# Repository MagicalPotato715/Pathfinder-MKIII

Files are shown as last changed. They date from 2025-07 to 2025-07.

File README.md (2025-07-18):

 ****PATHFINDER: MARK III****

-----

About: This is the PCB for the third generation of my project, Pathfinder. The goal for Pathfinder is to make a hexapod walking robot that is able to traverse in diverse and rugged terrain where conventional vehicles (e.g., cars, rovers) prove inefficient. The third generation of Pathfinder (Mark III) will feature significant upgrades from its predecessor (Mark II), including improved motors for speed and weight-bearing, an onboard 7.4V LiPo battery for tetherless power, an accelerometer, and an NRF chip for wireless communication.

Why: I began Pathfinder after my physics teacher encouraged me to join my school's science fair. I had always had an idea for a spider robot that I kept at the back of my mind, but this pushed me to bring it to life. Over the next few weeks, I poured hours every day into learning more about mechanical and electrical engineering. I also sought mentorship from the UC Berkeley Engineering Department and got connected with a Mech E & EECS graduate student.  Mark I of Pathfinder, a simple prototype/proof of concept, was churned out after 2 weeks, just in time for my district's science fair to win me 2nd place. Mark II was developed a few weeks later for the regional science fair. Mark III, the model this PCB is for, will be the culmination of my work over an entire year to be entered into next season's science fair.

(Note: The CAD model was created and fine-tuned over the course 3+ months that were before Highway began, so I didn't record the process in the journals.)

---

**In Depth: How It Works** (for all yall nerds out there)

- **PCB**
  - The PCB is, in essence, a servo driver. It is supposed to be placed on top of a Nucleo F446RE board, taking advantage of its Morpho pins that expose the MCU. The power comes in from a 7.4V 2S LiPo battery connected to the onboard XT60 (just a connector).
  - **Servos** Since the potential ampage could go up to ~10-15A, a pour is used to connect the battery to the 3 buck converters. Each buck converter steps down the battery power from 7.4V to 6V at 5A for 6 servos (two legs). This connection from the buck converters to the servo rails is led by another set of pours. The servos receive PWM input from 15 pins on the right morpho pins and 3 on the left.
  - **Power** The VIN from the XT60 is also connected to the F446RE's onboard VIN pin (it already has a regulator to step down to 3.3V). This power then comes out of the 3.3V pin and is fed to the NRF Chip and the Accelerometer.
  - **Accelerometer** The accelerometer used is the BNO055, an "INTELLIGENT ABSOLUTE ORIENTATION SENSOR, 9-AXIS SENSOR FUSION" (aka gyroscope & accelerometer and prob 9 other things). The BNO055 uses I2C and is connected to SDA & SCL. There is also a manual reset button connected to RST on the BNO055 just for funsies.
  - **NRF Chip** This is going to be used to communicate with the hand-held controller (to be made later). The NRF Chip is the NRF24L01_Breakout. NRF24L01_Breakout uses SPI and thus the MISO, MOSI, CSN, SCK, and CE pins on the F446RE (used on the left morpho pins).
  
- **Body**
  In-depth desc WIP
---

Screenshot 2025-07-18 at 9 36 13 AM  

Screenshot 2025-07-08 at 11 05 50 AM

Screenshot 2025-07-18 at 9 31 08 AM

Screenshot_2025-05-13_at_6 30 04_PM

|Component|Quantity|Model|Lowest Price|Link|
|---|---|---|---|---|
|LED|2|VLMR233T2V2-GS08|$0.35|[Link](https://www.aliexpress.com/item/1005008128628087.html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)|
|Button|2 (1x20pcs)|TL1240NQ1JBLK|$1.27|[Link](https://www.aliexpress.com/item/1005003938985112.html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)|
|Servo Motor|18 (2x10pcs)|MG996R|$30.81|[Link](https://www.aliexpress.com/item/1005007032811340.html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)|
|10uF Capacitor|7 (1x100pcs)|0805W106K250CC|$0.6|[Link](https://www.aliexpress.com/item/1626652703.html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)|
|10k Resistor|5 (1x100pcs)|CR0805-JW-103ELF|$0.35|[Link](https://www.aliexpress.com/item/1005006269805332.html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)|
|500 Resistor|2 (1x100pcs)|CR0805-FX-4990ELF|$0.35|[Link](https://www.aliexpress.com/item/1005006269805332.html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)|
|NRF Board|1|NRF24L01_Breakout|$0.58|[Link](https://www.aliexpress.com/item/1005005642753224.html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)|
|Schottky Resistor|3 (1x20pcs)|MBR1045S|$2.38|[Link](https://www.aliexpress.com/item/3256807600787150.html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)|
|Buck Converter|3 (1x5pcs)|RT8289GSP|$2.26|[Link](https://www.aliexpress.com/item/1005006319216009.html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)|
|47uF Capacitor|6 (1x10pcs)|6TAB47M|$10.30|[Link](https://www.aliexpress.com/item/3256807390659102.html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)|
|39k Resistor|3 (1x100pcs)|CR0805-FX-3832ELF|$0.35|[Link](https://www.aliexpress.com/item/1005006269805332.html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)|
|Developement Board|1|Nucleo F446RE|$25.13|[Link](https://www.aliexpress.com/item/3256808854818208.html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)|
|10uH Inductor|3 (1x10pcs)|EXL1V0505-100-R|$2.43|[Link](https://www.aliexpress.com/item/1005007254030376.html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)|
|XT60 Connector|1|XT60-M|$0.39|[Link](https://www.aliexpress.com/item/1005007103438736.html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)|
|Battery|1|7.4v 2s Lipo|$29.49|[Link](https://www.aliexpress.com/item/3256802810308498.html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)|
|0.1uF Capacitor|3 (1x100pcs)|0603B104K250SD|$0.95|[Link](https://www.aliexpress.com/item/1005003512666695.html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)|
|Accelerometer|1|BNO055|$29.32|[Link](https://www.aliexpress.com/item/3256809169239048.html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)|
|Female Headers|2 (1x10pcs)|PPPC192LFBN-RC|$0.89|[Link](https://www.aliexpress.com/item/4001198421663.html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)|
|Male Headers|18 (1x50pcs)|TS-103-G-A|$0.94|[Link](https://www.aliexpress.com/item/4000988113226.html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)|
|PCB Board|1| |$76.88|JLCPCB Order|

Total Components Price (+26.63 Shipping & tax): $223.39
PCB Price: $76.88
Total Price: $280.27

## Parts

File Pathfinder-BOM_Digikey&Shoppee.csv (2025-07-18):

Component | Quantity | Model | Lowest Price (unit) | Subtotal | Link
LED | 2 | VLMR233T2V2-GS08 | 0.51 | 1.02 | https://www.digikey.tw/en/products/detail/vishay-semiconductor-opto-division/VLMR233T2V2-GS08/3025490
Button | 2 | TL1240NQ1JBLK | 0.98 | 1.96 | https://www.digikey.tw/en/products/detail/e-switch/TL1240NQ1JBLK/1805479
Servo Motor | 18 | MG996R | 4.2 | 75.60 | https://tw.shp.ee/tT3prQu
10uF Capacitor | 7 | 0805W106K250CC | 0.04 | 0.28 | https://tw.shp.ee/vY3ZYgh
10k Resistor | 5 | CR0805-JW-103ELF | 0.10 | 0.50 | https://www.digikey.tw/en/products/detail/bourns-inc/CR0805-JW-103ELF/3593155
500 Resistor | 2 | CR0805-FX-4990ELF | 0.10 | 0.20 | https://www.digikey.tw/en/products/detail/bourns-inc/CR0805-FX-4990ELF/3784987
NRF Board | 1 | NRF24L01_Breakout | 1.00 | 1.00 | https://tw.shp.ee/tFocrzP
Schottky Resistor | 3 | MBR1045S | 1.07 | 3.21 | https://www.digikey.tw/en/products/detail/smc-diode-solutions/MBR1045S/5993230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
Buck Converter | 3 | RT8289GSP | 4.11 | 12.33 | https://www.digikey.tw/en/products/detail/richtek-usa-inc/RT8289GSP/2546068?s=N4IgTCBcDaIEoBUAcYkE4QF0C%2BQ
47uF Capacitor | 6 | 6TAB47M | 1.66 | 9.96 | https://www.digikey.tw/en/products/detail/panasonic-electronic-components/6TAB47M/4833040
38k Resistor | 3 | CR0805-FX-3832ELF | 0.10 | 0.30 | https://www.digikey.tw/en/products/detail/bourns-inc/CR0805-FX-3832ELF/3784908
Developement Board | 1 | NUCLEO-F446RE | 14.85 | 14.85 | https://www.digikey.tw/en/products/detail/stmicroelectronics/NUCLEO-F446RE/5347712
10uH Inductor | 3 | EXL1V0505-100-R | 0.69 | 2.07 | https://www.digikey.tw/en/products/detail/eaton-electronics-division/EXL1V0505-100-R/13912336
XT60 Connector | 1 | XT60-F | 1.57 | 1.57 | https://tw.shp.ee/Gx2Y8iE
0.1uF Capacitor | 3 | 0603B104K250SD | 1.70 | 5.10 | https://tw.shp.ee/weARm6H
Accelerometer | 1 | BNO055 | 38.46 | 38.46 | https://tw.shp.ee/19Ezxnb
Female Headers | 2 | PPPC192LFBN-RC | 2.05 | 4.1 | https://www.digikey.tw/en/products/detail/sullins-connector-solutions/PPPC192LFBN-RC/810258
Male Headers | 18 | TS-103-G-A | 1.27 | 22.86 | https://www.digikey.tw/en/products/detail/samtec-inc/TS-103-G-A/1105459
PCB Board | 1 |  | 76.88 | JLCPCB Order
Total |  |  |  | 245.29

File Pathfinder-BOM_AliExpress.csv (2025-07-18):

Component | Quantity | Model | Lowest Price | Link
LED | 2 | VLMR233T2V2-GS08 | $0.35 | https://www.aliexpress.com/item/1005008128628087.html
Button | 2 (1x20pcs) | TL1240NQ1JBLK | $1.27 | https://www.aliexpress.com/item/1005003938985112.html
Servo Motor | 18 (2x10pcs) | MG996R | $30.81 | https://www.aliexpress.com/item/1005007032811340.html
10uF Capacitor | 7 (1x100pcs) | 0805W106K250CC | $0.60 | https://www.aliexpress.com/item/1626652703.html
10k Resistor | 5 (1x100pcs) | CR0805-JW-103ELF | $0.35 | https://www.aliexpress.com/item/1005006269805332.html
500 Resistor | 2 (1x100pcs) | CR0805-FX-4990ELF | $0.35 | https://www.aliexpress.com/item/1005006269805332.html
NRF Board | 1 | NRF24L01_Breakout | $0.58 | https://www.aliexpress.com/item/1005005642753224.html
Schottky Resistor | 3 (1x20pcs) | MBR1045S | $2.38 | https://www.aliexpress.com/item/3256807600787150.html
Buck Converter | 3 (1x5pcs) | RT8289GSP | $2.26 | https://www.aliexpress.com/item/1005006319216009.html
47uF Capacitor | 6 (1x10pcs) | 6TAB47M | $10.30 | https://www.aliexpress.com/item/3256807390659102.html
39k Resistor | 3 (1x100pcs) | CR0805-FX-3832ELF | $0.35 | https://www.aliexpress.com/item/1005006269805332.html
Developement Board | 1 | Nucleo F446RE | $25.13 | https://www.aliexpress.com/item/3256808854818208.html
10uH Inductor | 3 (1x10pcs) | EXL1V0505-100-R | $2.43 | https://www.aliexpress.com/item/1005007254030376.html
XT60 Connector | 1 | XT60-M | $0.39 | https://www.aliexpress.com/item/1005007103438736.html
Battery | 1 | 7.4v 2s Lipo | $29.49 | https://www.aliexpress.com/item/3256802810308498.html
0.1uF Capacitor | 3 (1x100pcs) | 0603B104K250SD | $0.95 | https://www.aliexpress.com/item/1005003512666695.html
Accelerometer | 1 | BNO055 | $29.32 | https://www.aliexpress.com/item/3256809169239048.html
Female Headers | 2 (1x10pcs) | PPPC192LFBN-RC | $0.89 | https://www.aliexpress.com/item/4001198421663.html
Male Headers | 18 (1x50pcs) | TS-103-G-A | $0.94 | https://www.aliexpress.com/item/4000988113226.html
PCB Board | 1 |  | $76.88 | JLCPCB Order
Total |  |  | $280.27

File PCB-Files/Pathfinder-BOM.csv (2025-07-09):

Id | Designator | Footprint | Quantity | Designation | Supplier and ref
1 | D4,D5 | LED_miniPLCC_2315_Handsoldering | 2 | LED
2 | SW2,SW1 | SW_PUSH_6mm_H9.5mm | 2 | SW_Push
3 | Coxa2,Femur1,Tibia5,Tibia1,Femur3,Coxa4,Coxa5,Tibia3,Tibia2,Coxa3,Femur6,Femur4,Tibia4,Coxa6,Coxa1,Tibia6,Femur5,Femur2 | PinHeader_1x03_P2.54mm_Vertical | 18 | Motor_Servo
4 | C8,C5,C7,C13,C16,C4,C12 | C_0805_2012Metric | 7 | 10uF
5 | R7,R6,R4,R8,R2 | R_0805_2012Metric | 5 | 10k
6 | R9,R10 | R_0805_2012Metric | 2 | 500
7 | U2 | nRF24L01_Breakout | 1 | NRF24L01_Breakout
8 | D7,D1,D3 | MBR1045S | 3 | D_Schottky
9 | BuckConverterB1,BuckConverterC1,BuckConverterA1 | SOIC127P599X175-9N | 3 | ~
10 | C2,C3,C9,C15,C10,C14 | CAP_TA_B2_PAN | 6 | 47uF
11 | R5,R1,R3 | R_0805_2012Metric | 3 | 38k
12 | U1 | MODULE_NUCLEO-F446RE | 1 | NUCLEO-F446RE
13 | L3,L1,L2 | IND_EXL1V0505-100-R_COB | 3 | 10uH
14 | J1 | AMASS_XT60-M | 1 | XT60-M
15 | C11,C6,C1 | C_0603_1608Metric | 3 | 0.1uF
16 | Bno055 | BNO055 | 1 | ~

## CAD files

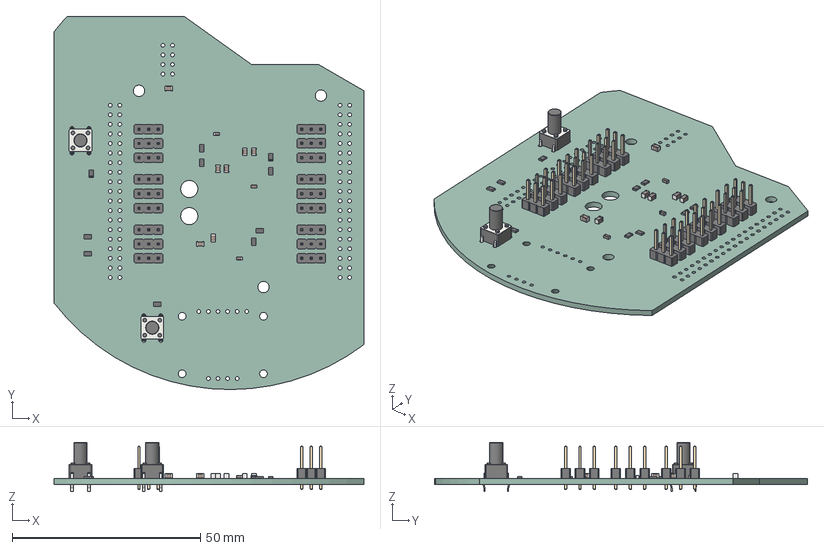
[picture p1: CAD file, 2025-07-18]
PCB-Files/Pathfinder.step
82.2 x 99.0 x 13.0 mm
SW_PUSH_6mm_H9.5mm x 2
PinHeader_1x03_P2.54mm_Vertical x 18
C_0805_2012Metric x 7
R_0805_2012Metric x 10
C_0603_1608Metric x 3
Pathfinder_PCB

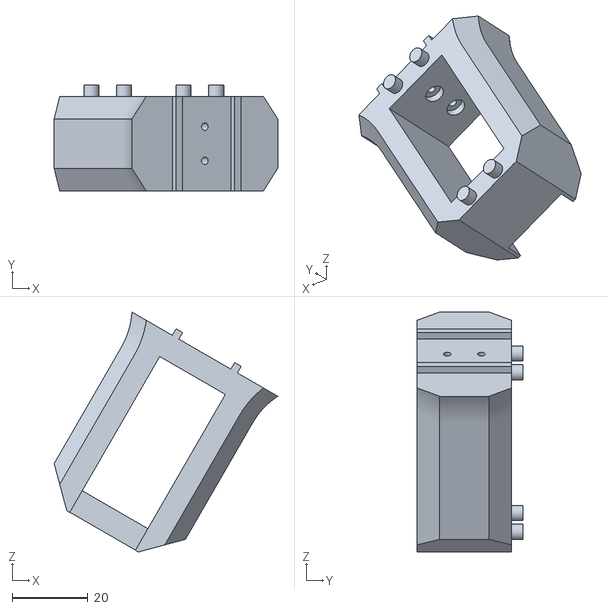
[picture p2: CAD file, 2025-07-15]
CAD-Files/Center Piece Copy 1 - Part 3.stl
59.0 x 28.0 x 63.3

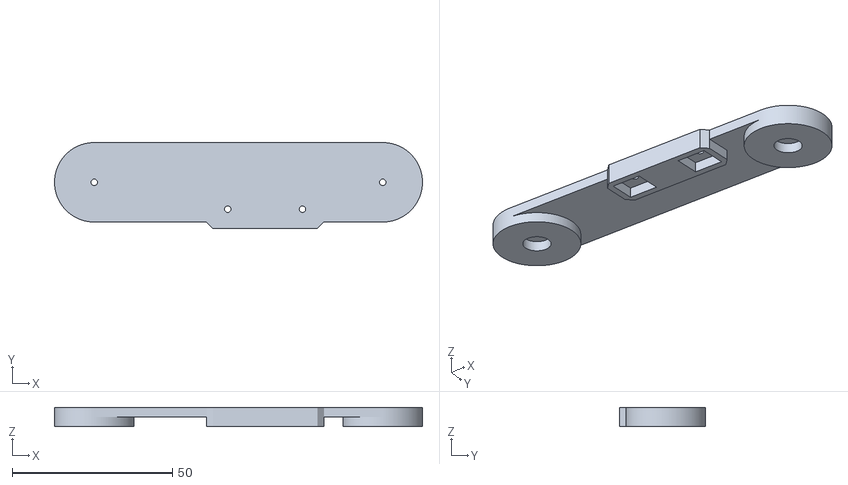
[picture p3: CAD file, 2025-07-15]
CAD-Files/Femur - Part 2.stl
114.8 x 26.8 x 6.00

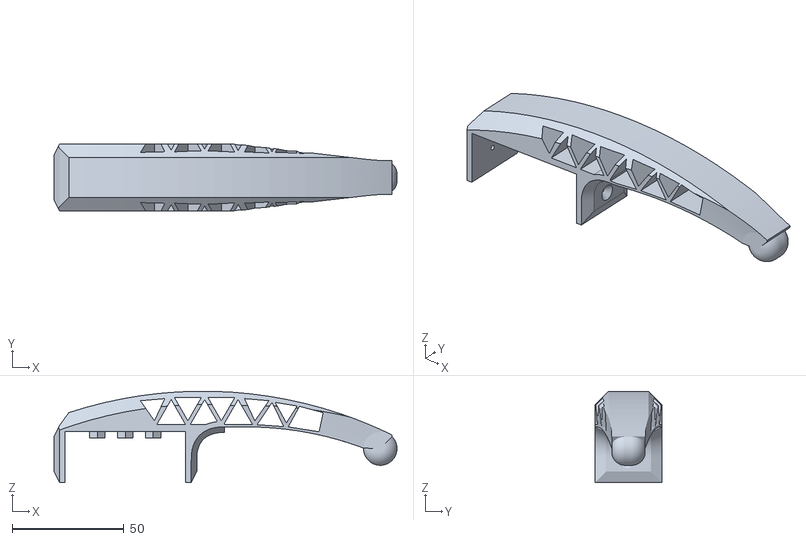
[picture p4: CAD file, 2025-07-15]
CAD-Files/Tibia.stl
153.7 x 30.0 x 41.0

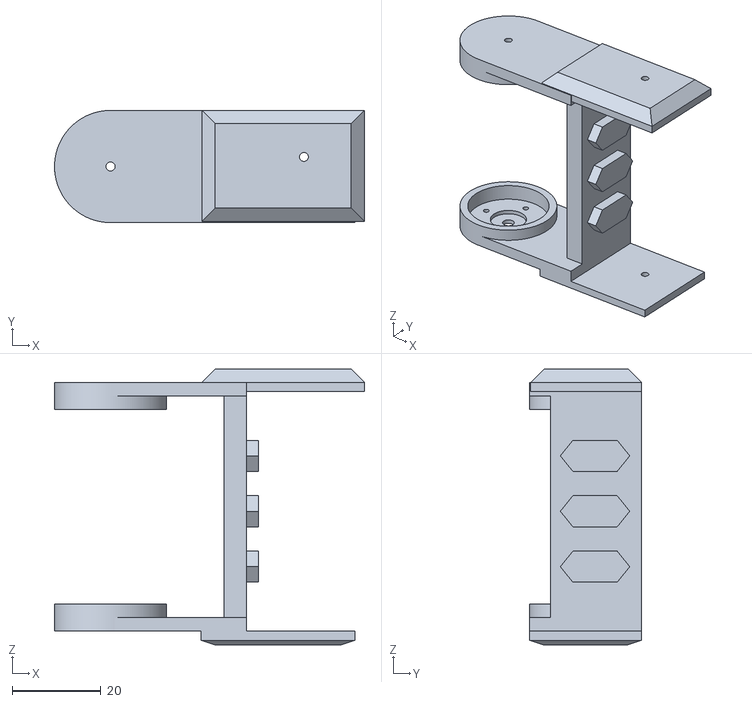
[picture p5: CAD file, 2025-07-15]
CAD-Files/Coxa - Part 4 (4).stl
69.9 x 25.3 x 62.2

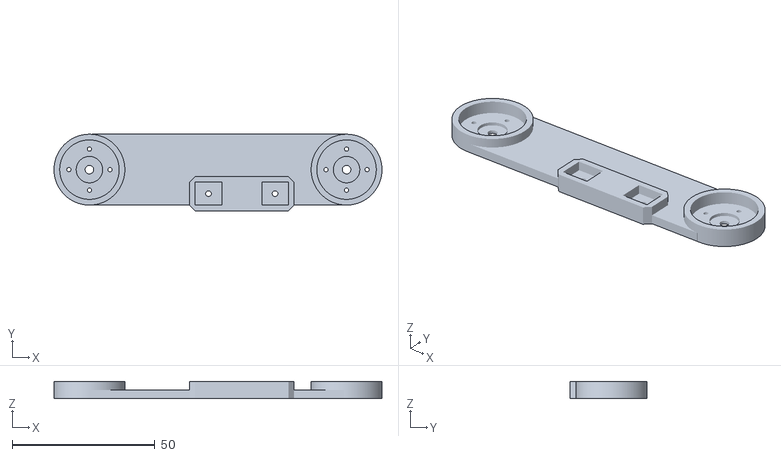
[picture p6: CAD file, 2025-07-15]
CAD-Files/Femur - Part 4.stl
114.8 x 26.8 x 6.00

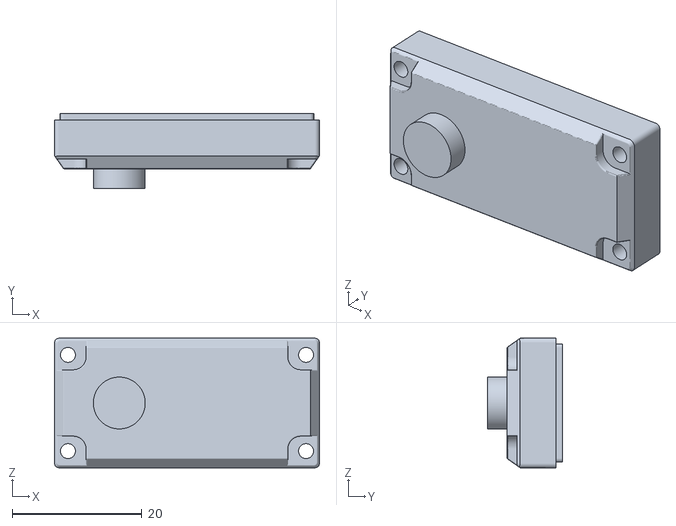
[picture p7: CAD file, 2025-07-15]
CAD-Files/Case Updated.stl
40.9 x 11.5 x 20.0

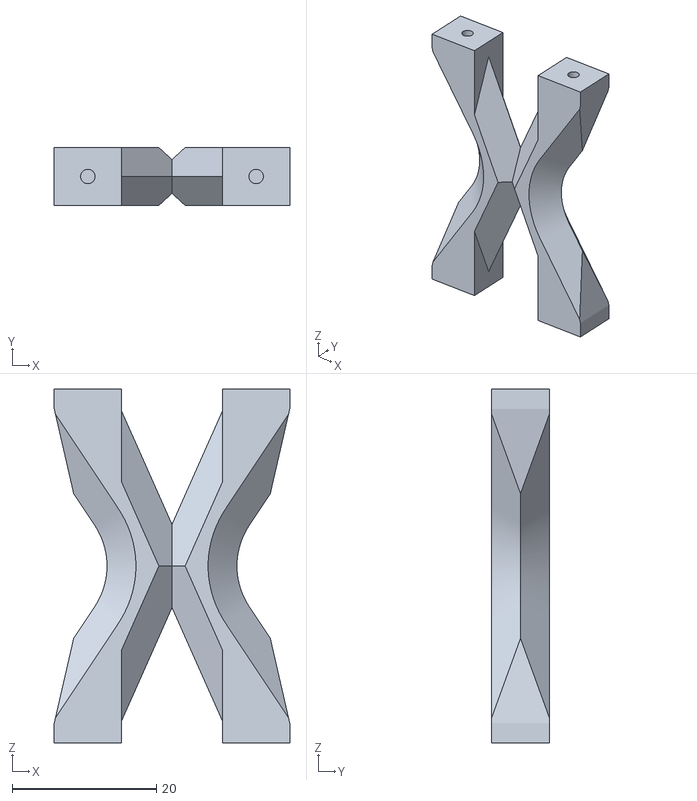
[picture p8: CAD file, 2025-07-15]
CAD-Files/Femur - Part 3.stl
32.6 x 8.00 x 49.0

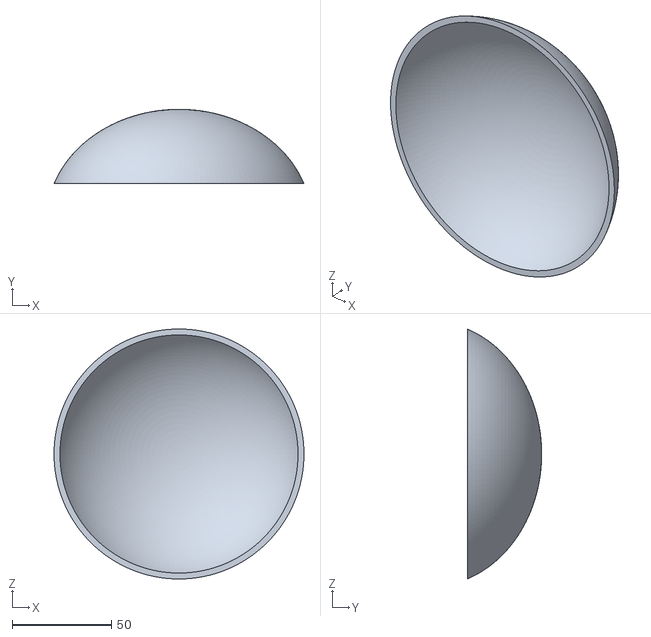
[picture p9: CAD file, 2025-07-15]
CAD-Files/Center Piece Copy 1 - Part 1.stl
126.0 x 37.5 x 126.0

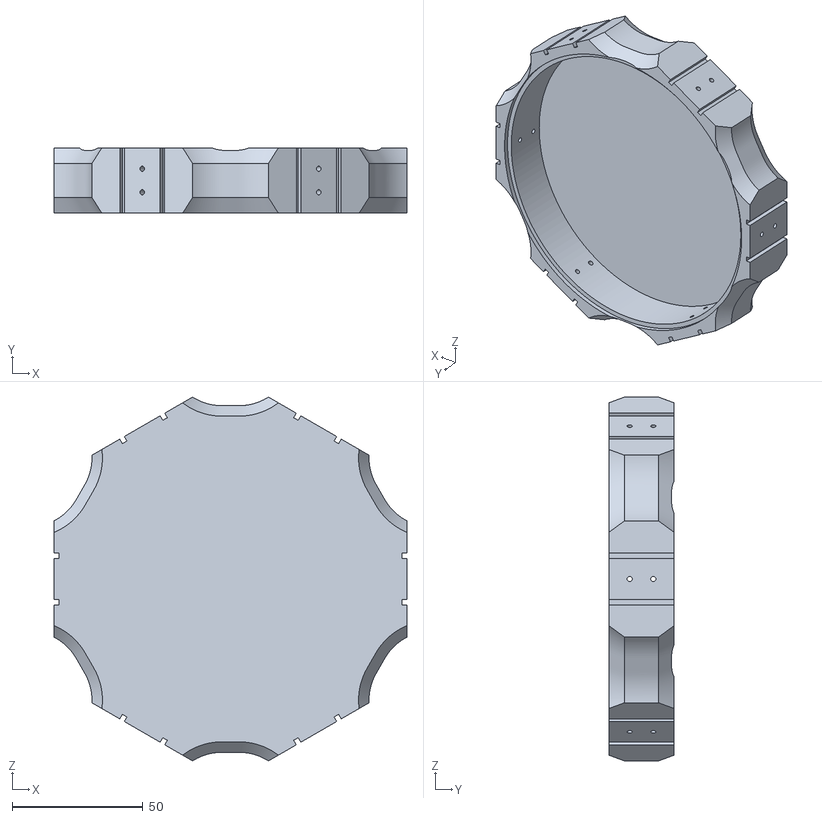
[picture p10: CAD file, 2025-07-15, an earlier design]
CAD-Files/Center Piece Copy 1 - Part 3 (4).stl
135.0 x 25.0 x 139.2

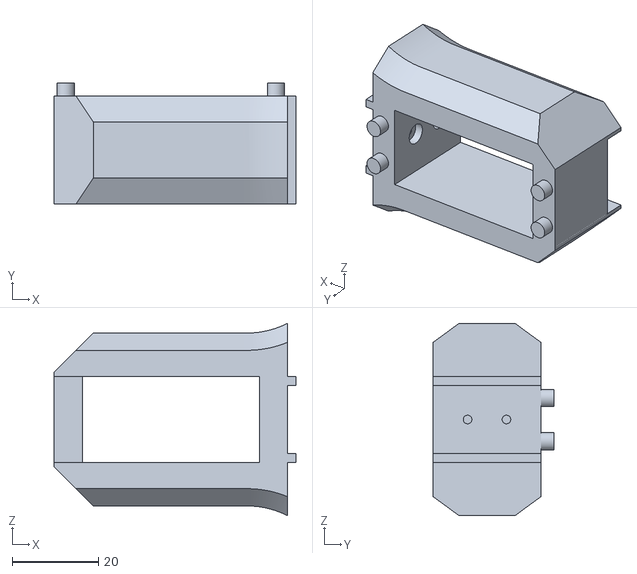
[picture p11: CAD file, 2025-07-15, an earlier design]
CAD-Files/Center Piece Copy 1 - Part 3 (6).stl
56.0 x 28.0 x 44.5

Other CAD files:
CAD-Files/Center Piece Copy 1 - Part 3 (5).stl
CAD-Files/Center Piece Copy 1 - Part 3 (1).stl
CAD-Files/Center Piece Copy 1 - Part 3 (3).stl
CAD-Files/Center Piece Copy 1 - Part 3 (2).stl

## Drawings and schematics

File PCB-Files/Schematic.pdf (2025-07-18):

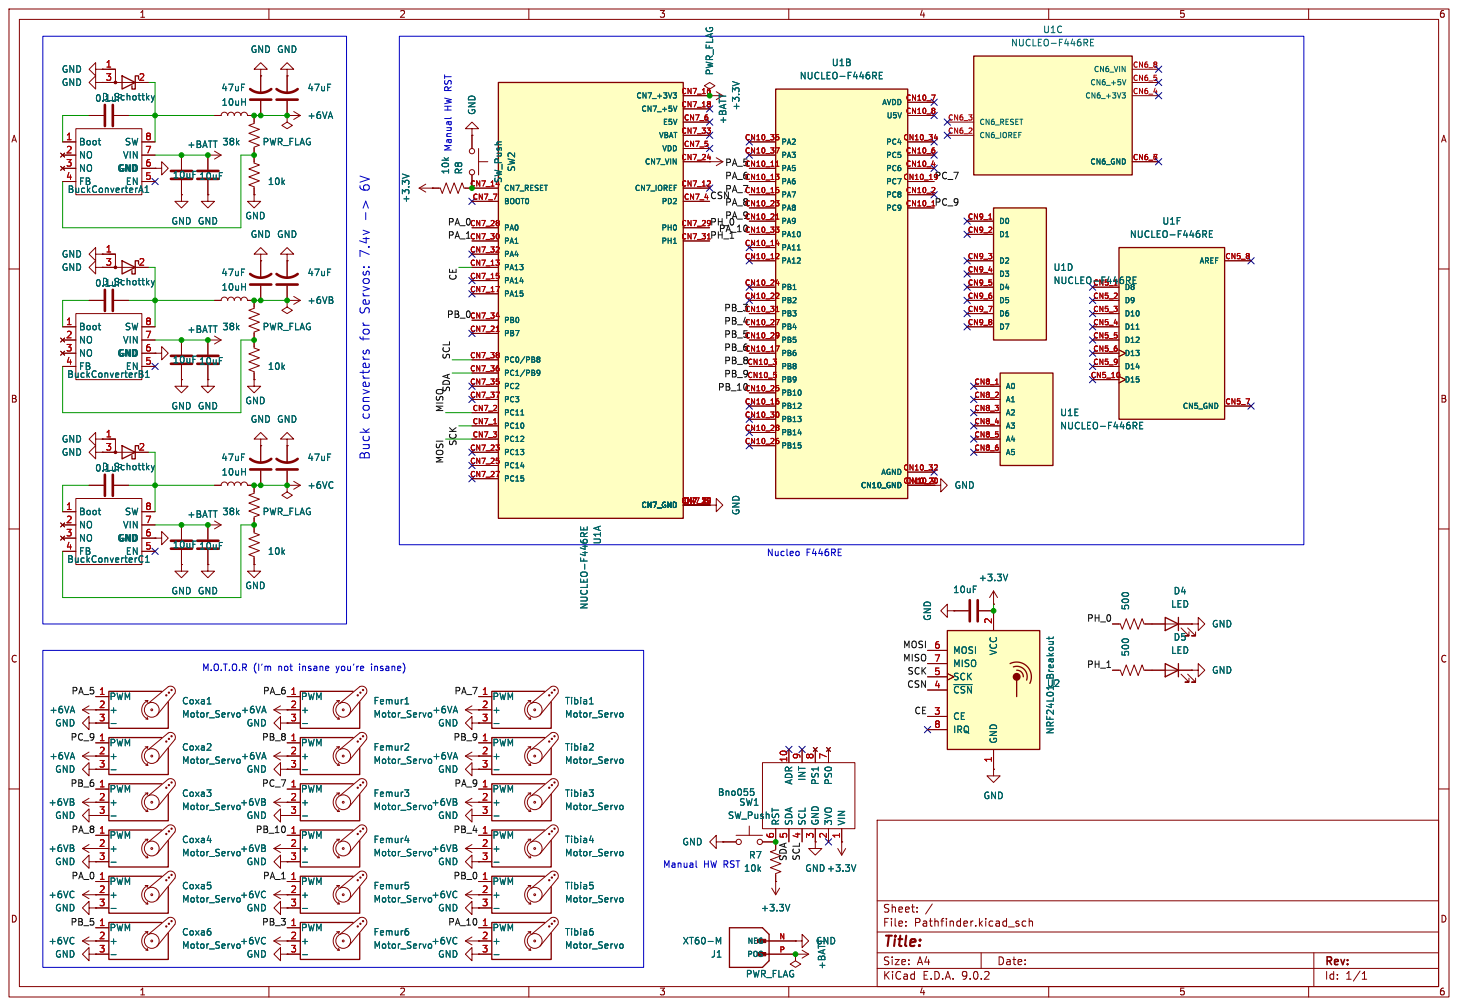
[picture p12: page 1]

Id: 1/1 Title: File: Pathfinder.kicad_sch Sheet: /

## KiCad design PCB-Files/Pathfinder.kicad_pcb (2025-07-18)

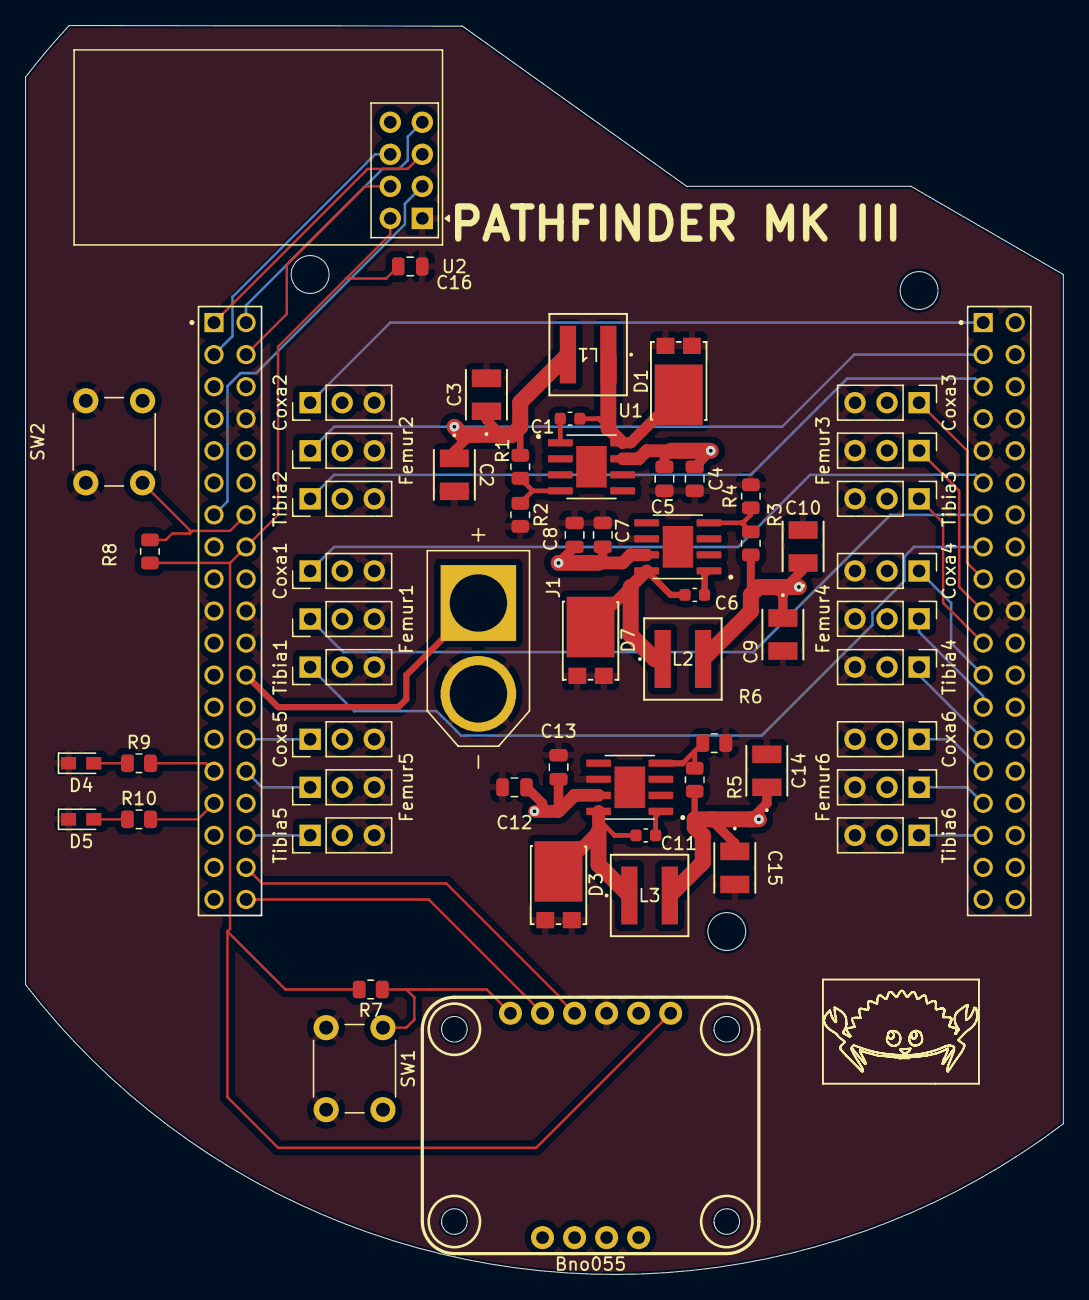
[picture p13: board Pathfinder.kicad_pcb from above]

Board: 4 copper layers, 82.2 x 99.0 mm, 61 parts (0 on the bottom side), 46 nets.

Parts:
Bno055: BNO055
BuckConverterA1: SOIC127P599X175-9N
BuckConverterB1: SOIC127P599X175-9N
BuckConverterC1: SOIC127P599X175-9N
C1, C6, C11: 0.1uF; C_0603_1608Metric
C2, C3, C9, C10, C14, C15: 47uF; CAP_TA_B2_PAN
C4, C5, C7, C8, C12, C13, C16: 10uF; C_0805_2012Metric
Coxa1, Coxa2, Coxa3, Coxa4, Coxa5, Coxa6: Motor_Servo; PinHeader_1x03_P2.54mm_Vertical
D1, D3, D7: D_Schottky; MBR1045S
D4, D5: LED; LED_miniPLCC_2315_Handsoldering
Femur1, Femur2, Femur3, Femur4, Femur5, Femur6: Motor_Servo; PinHeader_1x03_P2.54mm_Vertical
J1: XT60-M; AMASS_XT60-M
L1, L2, L3: 10uH; IND_EXL1V0505-100-R_COB
R1, R3, R5: 38k; R_0805_2012Metric
R2, R4, R6, R7, R8: 10k; R_0805_2012Metric
R9, R10: 500; R_0805_2012Metric
SW1, SW2: SW_Push; SW_PUSH_6mm_H9.5mm
Tibia1, Tibia2, Tibia3, Tibia4, Tibia5, Tibia6: Motor_Servo; PinHeader_1x03_P2.54mm_Vertical
U1: NUCLEO-F446RE; MODULE_NUCLEO-F446RE
U2: NRF24L01_Breakout; nRF24L01_Breakout

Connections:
+3.3V: Bno055.Vin, C16.1, R7.2, R8.2, U1.CN7_16 (CN7_+3V3), U2.2 (VCC)
+6VA: C2.1, C3.1, Coxa1.2 (+), Coxa2.2 (+), Femur1.2 (+), Femur2.2 (+), L1.2, R1.1, Tibia1.2 (+), Tibia2.2 (+)
+6VB: C9.1, C10.1, Coxa3.2 (+), Coxa4.2 (+), Femur3.2 (+), Femur4.2 (+), L2.2, R3.1, Tibia3.2 (+), Tibia4.2 (+)
+6VC: C14.1, C15.1, Coxa5.2 (+), Coxa6.2 (+), Femur5.2 (+), Femur6.2 (+), L3.2, R5.1, Tibia5.2 (+), Tibia6.2 (+)
+BATT: BuckConverterA1.7 (VIN), BuckConverterB1.7 (VIN), BuckConverterC1.7 (VIN), C4.1, C5.1, C7.1, C8.1, C12.1, C13.1, J1.P (POS), U1.CN7_24 (CN7_VIN)
/CE: U1.CN7_13 (PA13), U2.3 (CE)
/CSN: U1.CN7_4 (PD2), U2.4 (~CSN)
/MISO: U1.CN7_2 (PC11), U2.7 (MISO)
/MOSI: U1.CN7_3 (PC12), U2.6 (MOSI)
/PA_0: Coxa5.1 (PWM), U1.CN7_28 (PA0)
/PA_1: Femur5.1 (PWM), U1.CN7_30 (PA1)
/PA_5: Coxa1.1 (PWM), U1.CN10_11 (PA5)
/PA_6: Femur1.1 (PWM), U1.CN10_13 (PA6)
/PA_7: Tibia1.1 (PWM), U1.CN10_15 (PA7)
/PA_8: Coxa4.1 (PWM), U1.CN10_23 (PA8)
/PA_9: Tibia3.1 (PWM), U1.CN10_21 (PA9)
/PA_10: Tibia6.1 (PWM), U1.CN10_33 (PA10)
/PB_0: Tibia5.1 (PWM), U1.CN7_34 (PB0)
/PB_3: Femur6.1 (PWM), U1.CN10_31 (PB3)
/PB_4: Tibia4.1 (PWM), U1.CN10_27 (PB4)
/PB_5: Coxa6.1 (PWM), U1.CN10_29 (PB5)
/PB_6: Coxa3.1 (PWM), U1.CN10_17 (PB6)
/PB_8: Femur2.1 (PWM), U1.CN10_3 (PB8)
/PB_9: Tibia2.1 (PWM), U1.CN10_5 (PB9)
/PB_10: Femur4.1 (PWM), U1.CN10_25 (PB10)
/PC_7: Femur3.1 (PWM), U1.CN10_19 (PC7)
/PC_9: Coxa2.1 (PWM), U1.CN10_1 (PC9)
/PH_0: R9.2, U1.CN7_29 (PH0)
/PH_1: R10.2, U1.CN7_31 (PH1)
/SCK: U1.CN7_1 (PC10), U2.5 (SCK)
/SCL: Bno055.SCL, U1.CN7_38 (PC0/PB8)
/SDA: Bno055.SDA, U1.CN7_36 (PC1/PB9)
GND: Bno055.GND, BuckConverterA1.6 (GND), BuckConverterB1.6 (GND), BuckConverterC1.6 (GND), C2.2, C3.2, C4.2, C5.2, C7.2, C8.2, C9.2, C10.2, C12.2, C13.2, C14.2, C15.2, C16.2, Coxa1.3 (-), Coxa2.3 (-), Coxa3.3 (-), Coxa4.3 (-), Coxa5.3 (-), Coxa6.3 (-), D1.1 (A), D1.3 (A), D3.1 (A), D3.3 (A), D4.1 (K), D5.1 (K), D7.1 (A), D7.3 (A), Femur1.3 (-), Femur2.3 (-), Femur3.3 (-), Femur4.3 (-), Femur5.3 (-), Femur6.3 (-), J1.N (NEG), R2.2, R4.2, R6.2, SW1.2, SW2.2, Tibia1.3 (-), Tibia2.3 (-), Tibia3.3 (-), Tibia4.3 (-), Tibia5.3 (-), Tibia6.3 (-), U1.CN7_8 (CN7_GND), U1.CN7_19 (CN7_GND), U1.CN7_20 (CN7_GND), U1.CN7_22 (CN7_GND), U1.CN10_9 (CN10_GND), U1.CN10_20 (CN10_GND), U2.1 (GND)
unnamed: Bno055.RST, R7.1, SW1.1
unnamed: BuckConverterA1.1 (Boot), C1.1
unnamed: BuckConverterA1.4 (FB), R1.2, R2.1
unnamed: BuckConverterA1.8 (SW), C1.2, D1.2 (K), L1.1
unnamed: BuckConverterB1.1 (Boot), C6.1
unnamed: BuckConverterB1.4 (FB), R3.2, R4.1
unnamed: BuckConverterB1.8 (SW), C6.2, D7.2 (K), L2.1
unnamed: BuckConverterC1.1 (Boot), C11.1
unnamed: BuckConverterC1.4 (FB), R5.2, R6.1
unnamed: BuckConverterC1.8 (SW), C11.2, D3.2 (K), L3.1
unnamed: D4.2 (A), R9.1
unnamed: D5.2 (A), R10.1
unnamed: R8.1, SW2.1, U1.CN7_14 (CN7_RESET)

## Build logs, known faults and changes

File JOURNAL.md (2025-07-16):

---
title: Pathfinder Mark-III
author: Calvin Hung
Description: This project is the third edition of my hexapod Pathfinder for the science fair. It will be a significant upgrade from Mk-II, having significantly stronger motors a complex buck converter power control. Additionally, I also want it to feature remote control, and a good inverse kinematics system so that I won't have to hard code in movements.
created_at: 6/18/25
Total Time Spent: 44 hours
---

# April 22nd: Research and Designing the First CAD models of Mark III

For the Mark III, I aimed for a total overhaul of the Mark II (shown below), primarily to incorporate more powerful servo motors, have better walking gaits, and achieve a more conventional hexapod appearance.



I took a lot of inspiration from hexapods like the MX-Phoenix and Aecert Robotics' hexapods, and held them as my goal for the final appearance. 

MX-Phoenix:
MX-Phoenix-1280x720
Aecert Robotics:
Hexapod1

So, clearly there was a lot of work to be done. The first objective is to create a way to mount the servos into the 3D printed chassis (I'm using MG996R's which don't have easy screw holes to mount to). My first idea was to follow Aecert Robotics and make a sort of sleeve for the servo (shown below). However, with this, there would only be a single point of connection to each motor (at the horn); if left alone, this would be really unstable. I added an extension to the bottom of the servo (in line with the gear) to act as another rotation point.

Screenshot 2025-07-15 at 7 13 28 PM

Issues: Bottom mount part is very annoying to print; very likely to mess up. The tolerance of the sleeve is very tight because slightly too small would prevent the motor from fitting, and too big would prevent the mounting pegs from fitting. Additionally, the bottom mount doesn't secure well to the sleeve and is thus unable to bear weight.

**Total time spent: 2hrs**

# April 24rd: Redesign and Femur Has Been Created

The bottom mount is proving to be inefficient, so I decided to redesign it. Since mounting was the issue, I decided to make the peg part of the bottom piece of the motor case (it can be removed by taking out the screws). 

Screenshot 2025-07-15 at 7 21 31 PM

Next, I started to make the Tibia because it looked like the simplest part. I started with simple connecting bars to each mounting point on either side of the motors. The actual mounting of the servo motors would be through the screw holes on the motor horns. Finally, I made a cool-looking X middle connector with a bunch of chamfers. I later decided to move the center connector slightly up, as to avoid issues with it hitting the motor.

Screenshot_2025-04-21_at_9 42 26_PM

Issues: All of the femur parts had to be sized up 102% in slicing in order to fit with the servo horn I was testing it with. Also, the X connector had a really, really tight fit with the side bars.

**Total time spent: 2hrs**

# April 25th: Making the Tibia

Today I designed the Tibia. Because I wanted to make it into a curve (so it looks cool), I used ChatGPT to find that the ideal absolute length of the tibia is 130mm. Next, I used a straight line from the servo case outwards with a curve on top to begin making the leg. I had to be careful to place the start of the line where the rotating gear would be. I added screw holes and protruding holes in the tibia design to ensure a strong connection with the servo mount. After, I changed the tip of the tibia into a ball because it would be brought down on different angles. This would make sure that there wouldn't be much "imbalance" where based on the angle where the tibia is brought down.

Screenshot 2025-07-16 at 11 05 18 AM

Issues: the mounting protrusions don't really fit too well (tolerancing). While printing, the bottom side of the tibia often has slight deformations.

**Total time spent: 1hr**

# April 26th: Making the Coxa

To finish off the leg, I finally made the Coxa (base joint). I just made a simple connector between two servo holders with different orientations, while using the same mounting protrusions 

Upon printing, I realized there were a few errors. With tolerancing, the servo horn part had to be scaled up 102% in slicing, while the servo mounting had to be exact. To fix this, I manually sized up the horn coupler in CAD. With printing, there isn't an easy way to print the coxa, since either the horn coupler would have to be printed sideways, or there would be a massive overhang. Finally, the original design I made was facing the wrong direction...

Screenshot 2025-07-16 at 11 20 33 AM

**Total time spent: 1hr**

# May 3rd & 4th: Making the Centerpiece

For the centerpiece, I began by making a simple connector to hold the coxa servo motors. I made a sort of pie slice that would connect to the motors and copied it around to make a hexagon. I also added a simple dome to cover up the center. Later, I changed the mounting to just have the motor sleeve as a part of the centerpiece. However, with this design, I wouldn't be able to fit it on my A1 Mini printer. 

Screenshot 2025-07-16 at 11 34 57 AM

To make the centerpiece fit on the build plate, I decided to have the motor-mounts print separately and screw on later. I also added grooves to ensure a stronger connection.



Issues: The grooves don't print sharply, so they don't make a complete seal. Upon printing, I realized that the center hole isn't large enough to fit my MCU.

Screenshot 2025-07-16 at 11 41 29 AM

With this, the hardware is complete and I can begin with the electronics / code.

**Total time spent: 3hrs**

# May 11th: Playing Around With Inverse Kinematics

I'm starting to play around with how I want Mark III to move. With the earlier models, I just used hardcoded angles for movement, but for Mark III I want to use inverse kinematics for smooth, new movement.

Turns out, inverse kinematics is quite simple! You use known segment lengths as well as a relative destination to use trigonometry to solve for the angles. However, with my first attempts at IK, the leg wouldn't move directly to the destination and would move wildly. To fix this, I made the leg move in smaller ticks in a straight line so it would just follow points along a line instead of just going to the destination.

Screenshot 2025-07-16 at 11 51 30 AM

2 Dimensions:
https://github.com/user-attachments/assets/a3eb9b45-d414-4b76-a091-abc09decaa17

3 Dimensions:
https://github.com/user-attachments/assets/2f3c27b4-28a0-40f4-89b9-6f2e65d93d94

**Total time spent: 3hrs**

# June 18th: Finished the Box Plot

I finally finalized my box plot for the PCB! It's also somewhat heavily inspired by Aecert Robotics' design, but I removed the pressure sensors because I don't see the point in them. Also, I'm going to use the Bno055 as the gyro because the one Aecert uses is kind of bad :/. However, I want this design to be original - uniquely mine, so I'm going to base the power from better buck converters, have the main MCU be a Nucleo F446re, and use more affordable budget servos.

Screenshot 2025-07-07 at 8 25 38 PM

**Total time spent: 4hrs**

# June 20th: Made first Schematic :D

The box plot makes wiring so easy! Passives like capacitors are annoying, though (but that's what ChatGPT is for). Good thing that datasheets give circuit diagrams, though! I'm having a hard time comprehending some parts of the circuits, like resistor dividers, but I'm slowly learning. Additionally, there are a bunch of ERC errors, and I don't think the nucleo footprint has nearly enough pins? Finding symbols/footprints was a massive pain, too. For example, for stuff like the passives, I kinda don't know what footprint to use because there are so many and I don't want to use the wrong one! Also, for things like the Bno055, all I could find on the internet were symbols of the chip itself, not the breakout board. I ended up having to make my own symbol.

Screenshot_2025-06-24_at_11 07 03_PM

**Total time spent: 3hrs**

# June 25th: Finally fixed my schematic ugh -_-

I finally found the rest of the Nucleo footprint(s)! Turns out, there are 6 different parts. Although, I'm only using the two that have morpho pins XD. Also thought to clean up the space a little. The buck converter passive circuit was becoming confusing so I just wired it. The servo motor array is the bane of my existence - so annoying to rearrange. An annoying thing is, each pin has like 5 different purposes and I can't find any concrete "this pin does specifically PWM/UART/I2C". Despite that, I CAN FINALLY START MAKING THE LAYOUT.

Screenshot_2025-06-25_at_12 31 23_PM

**Total time spent: 5hrs**

# June 26th: Layout Designing go brrr (SO MANY ERRORS UGH)

The buck converters' passives are sooooo annoying. I have to place so many things so many times. I'm also starting to realize I might not have enough space (maybe it was a bad idea to use ChatGPT to find footprints). I'm going to use something like Digikey to find new footprints for everything. Also, the servo --> PWM connections are all over the place (rearranging them is going to be a painnnnnnnn). I genuinely don't think I have enough space for the PCA servo driver, so I might get rid of it. Also, I don't know how to route power because 15 amps is a lot and my trace calculator said it has to be 300 mils...

Screenshot_2025-07-02_at_9 47 05_AM

**Total time spent: 3hrs**

# June 27th: Layout Designing go brrr - Take 2

I finally got a more optimized power system!!! Also, I found a way to fit everything on the board. Turns out that the footprints that ChatGPT gave me were wayyyy too big to fit. However, I do think that I'm placing things a little close together (in order to fit everything on the board) that there might be heat interference or smth. Routing is going to be fun!

Screenshot_2025-07-02_at_11 01 49_AM

**Total time spent: 5hrs**

# June 30th: Layout Designing go brrr (fml)

I HATE DRC. IT TEARS APART MY HOPES AND DREAMS. Routing was fun while it lasted, but there. were. so. many. errors.............. I feel like I don't know how big I should make the buck converter traces. My calculator said that they need to be crazy wide (which cannot fit on the VERY small space that I have), but ChatGPT (that I kind of don't trust anymore) reassured me that the short length of the traces would negate damage or something.(Also, I realized I can use pours for the power :O)

Screenshot_2025-07-03_at_10 24 26_AM
Screenshot_2025-07-02_at_12 29 06_PM

**Total time spent: 6hrs**

# July 1st: DRC PASSED!

After a lot of adjustments, all the DRC errors are now gonnnneeee!!!! I also learned about and implemented JLCPCB-specific design rules. Most of my errors consisted of: courtyard overlaps from components being close together, clearance issues of traces because the Kicad auto-route feature (I discovered) is based on a preset clearance that is just shy of the JLCPCB clearance, and some miscellaneous footprint/net errors. However, I'm still concerned on whether the servo voltage pours / vias will be able to carry the current. Prob a few tweaks left, but almost done!

Screenshot_2025-07-03_at_11 26 27_AM

Screenshot_2025-07-03_at_11 26 54_AM

**Total time spent: 2hrs**

# July 7th: I'M DONE

I moved around the layout and increased the trace width of the buck converter circuits. I uploaded my schematic and designs onto several Kicad communities for final insight. Additionally, I also exported a 3d model of the PCB from kicad into OnShape CAD to check if it would physically fit. I also fully mapped out all of the necessary components in Digikey to the correct dimensions and requirements I need. I think I'm ready. I'm confident with the board and it's ready to be made!

Screenshot 2025-07-07 at 8 54 44 PM
Screenshot 2025-07-07 at 8 55 07 PM

**Total time spent: ~2 hrs**
